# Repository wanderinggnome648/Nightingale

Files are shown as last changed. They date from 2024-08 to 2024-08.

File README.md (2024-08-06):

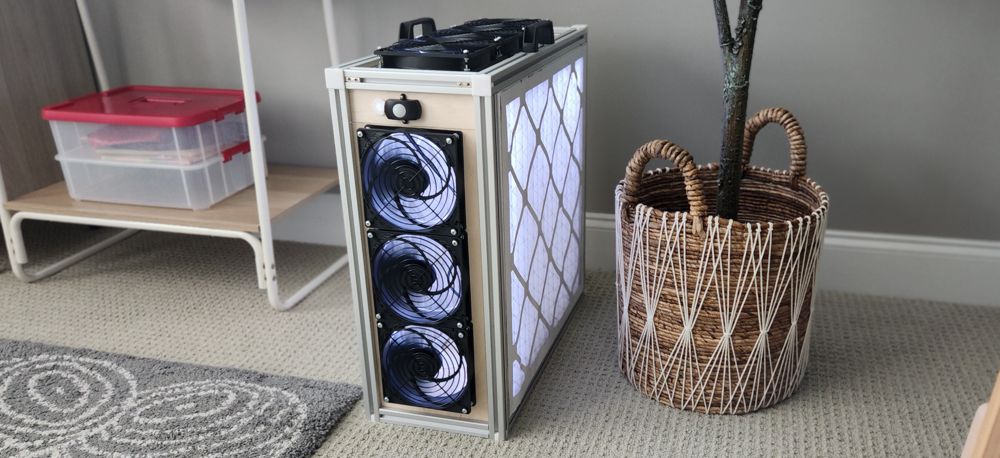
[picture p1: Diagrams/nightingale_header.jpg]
Product image


# The Nightingale: An Open-Source, Ultra-Quiet, Automatic, Permanent, Effective Air Purifier With Low Maintenance Costs

A PC-fan based air purifier design, the Nightingale's major features are:  
- **Effective**: Purifies air through two 20x20x2 MERV 13 air filters that are efficient at removing pollen, dust, and infectious aerosols, but have very high air flow.  
- **Ultra-Quiet**: No need to turn it down or off due to noise because you'll barely know it's running. Uses PC fans designed to push a high volume of air quietly. 
- **Permanent**: Uses a strong extruded aluminum frame that is a standard profile (1"x1") and easy to source from several manufacturers. 
- **Automatic**: Turns on when people are present and off when people leave. Always runs at max speed. Nothing to configure (or misconfigure). If it's plugged in, it's on. 
- **Visual Indicator**: Because the PC fans are so quiet, you might not even know it's on, so energy-efficient, interior lights indicate it is purifying. 
- **Easy Filter Change**: When you change the filters simply pop them off the side and replace. No disassembly required.
- **Cheap Maintenance**: No pricey filter replacement costs. Simply use standard MERV 13, 20x20x2 furnace filters commonly available in the US that cost around $10-$15 per filter (or less when purchased in bulk). Change yearly or after wildfire events. 
- **Standard Parts**: If you have a problem, you can fix it yourself. 
- **Open-Source**: No vendor lock-in. Build it. It's yours. 
- **Low Energy Consumption** Consumes only enough electricity for six PC fans and energy-efficient LED lighting. Turns off when the room is empty. 
- **Slim Design**: About the size of a desktop computer, it doesn't take up much space. 
- **Easy Wiring**: Uses standard connectors interior connectors (DC) that plug together. No soldering required.  

# Release Notes

## Version 1 - Baseline
Released on August 4, 2024. 

# Materials

You can likely do a better job sourcing materials in the quantity you need and obtaining a lower price. This is mostly just a list of all the items you would need to build a box and their approximate cost. 

## Aluminum Frame

Tnutz is a supplier of extruded aluminum. You can order specific lengths pre-cut. It takes about 5-8 days for processing. We use 1" x 1" T-slot frame, which is also known as 1010 T-slot frame. 

| Quantity | Type | Length | Fractional length | Total Length | Machining for one end | Machining for other end | Link  |
|---|---|---|---|---|---|---|---|
| 8 | 1"x1" | 20" | 0.500" |  20.5" | No machining | No machining | [LINK](https://www.tnutz.com/product/ex-1010/?attribute_pa_length-in=20&attribute_pa_fractional-length=0-500-1-2)
| 4 | 1"x1" | 7" | 0.063" (1/16) |  7.063" | No machining | No machining | [LINK](https://www.tnutz.com/product/ex-1010/?attribute_pa_length-in=7&attribute_pa_fractional-length=0-063-1-16)

## Panels 

We use 1/4" unfinished plywood for the panels because it's an inexpensive, durable material that is easy to find. You can source plywood in 4" x 8" sheets from any hardware store and then cut them down to manageable sheets using a table saw. Alternatively, MakerStock sources plywood in smaller sizes that is ideal for Glowforge laser cutting.  

| Quantity | Type | Thickness | Size | Cost/Piece | Link  |
| --- | ----- | ---- | ---- | -----  | -----  |
| 4 | Baltic Birch Plywood | 1/4" | 12x20 | $4.25/sheet |  [LINK](https://makerstock.com/products/baltic-birch-plywood?variant=32477598580833)  |

### Glowforge Laser Cutter
The Glowforge is a popular small laser cutter. The Glowforge size is slightly too small for the exact panel size that we need, so we break each panel into two parts -- the main part and a additional slat. 

See the LaserCut/SmallLaser folder for SVG files. Note that two of the panels are duplicates and so you need to cut them twice. 

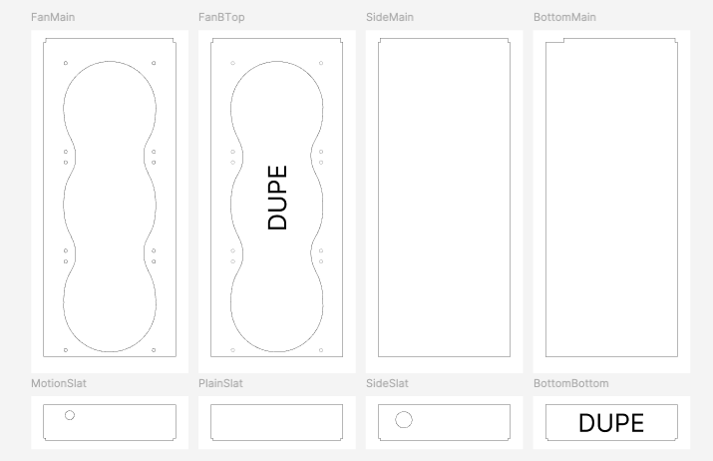
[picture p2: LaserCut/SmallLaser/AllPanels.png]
Diagram of all panels


To minimize burning of the material, we highly recommend covering the top face of the material with masking tape. Also, after cutting, we recommend sanding edges and inside the holes to eliminate the smoke smell. You don't want a purifier that smells like smoke!

Also, I'm not perfectly happy with the fit of the panels in the split design, and when I make my next few, I'll probably tweak the size a bit. It's tricky: Too big and you risk not fitting into the grooves. Too small, and it wobbles more than I'd like. Feel free to measure it yourself and iterate to get your perfect panel fit. If you find a better fit, let me know. 

### Large Laser Cutter
With a larger laser cutter, you can cut the entire panel in one piece. 
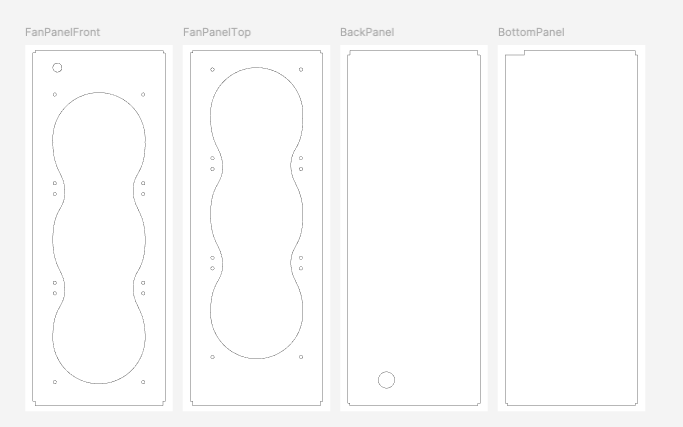
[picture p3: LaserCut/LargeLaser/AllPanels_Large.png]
Diagram of all panels


To minimize burning of the material, we highly recommend covering the material with masking tape. Also, after cutting, we recommend sanding edges and inside the holes to eliminate the smoke smell. You don't want a purifier that smells like smoke. 

### CNC
Instead of laser cutting, you can use a CNC to cut the panels. This is preferred to avoid having to sand off burnt material. Refer to the large laser cutter files for panel sizes or the primitives folder. 

*More instructions for CNC coming soon!*

## 3D Printed Components

Required
| Quantity | Item | Purpose | Filename | Image | 
| --- | ----- | -----| ----- | --- |
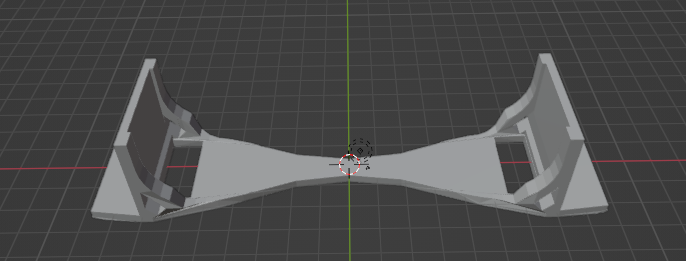
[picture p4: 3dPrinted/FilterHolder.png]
Filter holder
| 8 |  Filter Holder | Because the fans are mounted outside, the filter needs something to rest against | 3dPrinted\FilterHolder.stl | 

Optional
| Quantity | Item | Purpose | Filename | Image | 
| --- | ----- | -----| ----- | ---|
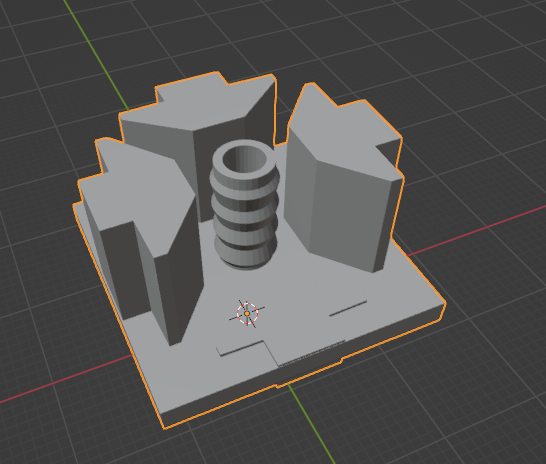
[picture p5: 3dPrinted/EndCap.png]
End Cap
| 8 |  End Cap | Cover sharp edges / protect scratches | 3dPrinted\EndCap.stl | 
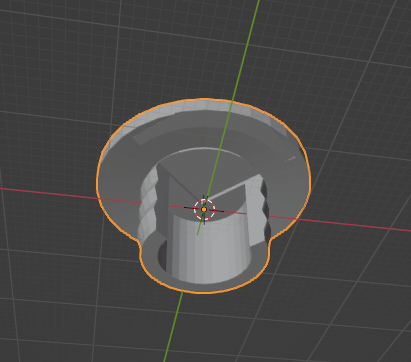
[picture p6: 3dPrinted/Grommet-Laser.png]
Grommet
| 1 | Grommet | Cover the hole where the motion sensor runs| 3dPrinter\Grommet-Laser.stl | 

NOTE: The end cap is a standard part and can be obtained elsewhere from TNutz, 80/20, and Amazon. Ensure the cap is 1"x1" (10 series, aka 1010). Also, you can get a rubber grommet from a hardware store.

## Interior Components 
| Quantity | Item | Description | Cost | Link  |
| --- | -----| --- | ---- | ----- |
| 1 | 5-Pack of Artic P14 PC Fans | Discounted pack of 5 fans | $35 | [LINK](https://www.amazon.com/dp/B07HC9ZWDN?psc=1&ref=ppx_yo2ov_dt_b_product_details) |
| 1 | Artic P14 PC Fans | Single P14 PC Fan (to make 6 total) | $16 | [LINK](https://www.amazon.com/dp/B07GZJY4TM?psc=1&ref=ppx_yo2ov_dt_b_product_details) |
| 2 | 3-pack of 140 mm fan grills | Covers the fan for safety | $9 | [LINK](https://www.amazon.com/dp/B01BW21DXC?psc=1&ref=ppx_yo2ov_dt_b_product_details)
| 1 | Adafruit DC Barrel Adapter | Using a 1" hole, this screws on the panel and provides a nice way to plug in the outside AC/DC power adapter | $3 plus shipping | [LINK](https://www.adafruit.com/product/610)
| 1 | AC/DC Adapter | Needs to be compatible with power where you are plugging it in (normally 110 volts in the US) and change to 12 volt, ~2 amp DC power | $5/each | [LINK](https://www.amazon.com/dp/B077PW5JC3?ref=ppx_yo2ov_dt_b_product_details&th=1)
| 1 | PWM Fan Hub | Connects all the fans to single power cable | $6 | [LINK](https://www.amazon.com/dp/B08C79CQH5?psc=1&ref=ppx_yo2ov_dt_b_product_details)
| 1 | DC Power 1 Female to 2 Male Y-Splitter | Splits DC power into two for lights and fan hub | $2 | [LINK](https://www.amazon.com/Splitter-Adapter-Y-Cable-Security-Parking/dp/B07J28SX6Y?th=1)
| 1 | PIR Motion Sensor | Activates the circuit when motion is detected | $6/each | [LINK](https://www.amazon.com/dp/B09PHHZMQN?psc=1&ref=ppx_yo2ov_dt_b_product_details)
| 1 | DC Extension Cable | Runs from the back of the unit to the front, where the motion sensor sits | $6 | [LINK](https://www.amazon.com/Power-Extension-Cable-5-5mm-Female/dp/B08176VFJ5?th=1) 
| 1 | DC to 4 Pin Fan Power | Converts DC power to 4 pin for the fans | $7 | [LINK](https://www.amazon.com/dp/B085S3Q7VH?psc=1&ref=ppx_yo2ov_dt_b_product_details)
| 1 | DC to LED light connector | Connects DC power to 2 pin LED lights that are 8 mm wide | $1/each | [LINK](https://www.amazon.com/dp/B01DM7F8O0?psc=1&ref=ppx_yo2ov_dt_b_product_details)
| 1 | String of 8mm LED lights | Any solid color, can be cut at specific intervals | $12 | [LINK](https://www.amazon.com/gp/product/B075LB9HK2/ref=ppx_yo_dt_b_search_asin_title?ie=UTF8&th=1)
| 1 | 20-pack of 1010 L-Shape Corner Connectors | Used to connect the aluminum pieces into a box | $28 | [LINK](https://www.amazon.com/dp/B09F67JQR1)
| 1 | 30-count M4 x 40-mm machine screws | To attach the grill to the fans and the fans to the panel, you need some relatively long machine screws. I think this is the right length to go the entire length of the fan. However, I did it the harder way with 2 screws and bolts per hole. If you find out 40mm is wrong (or you find the right imperial version, let me know) | $6 | [LINK](https://www.lowes.com/pd/Hillman-4mm-0-7-x-40mm-Phillips-Slotted-Combination-Drive-Machine-Screws-30-Count/999994818)
| 2 | 16-count M4 nuts | To attach the grill to the fans and the fans to the panel, you need some relatively long machine screws | $3/each | [LINK](https://www.lowes.com/pd/Hillman-4mm-x-0-7-Zinc-Plated-Steel-Hex-Nut-16-Count/999995424)
| 2 | Plastic Handle | Screws into the wood slot and makes carrying the unit easier. | $5/each | [LINK](https://www.tnutz.com/product/han-015/)
| 2 | Tiny wood screws | To mount the motion sensor into the wood panel, you need some very small screws. Recommended size is about <.5" in length. You likely have something already that would work.

## Filter
| Quantity | Item | Description | Cost | Link  |
| --- | -----| --- | ---- | ----- |
| 2 | MERV 13 20x20x2 Furnace Filter | Filter medium | $10/each | [LINK](https://www.amazon.com/gp/product/B0BL4XBTLN?th=1) |

Note: 20x20 furnace filters are NOT 20" long. They are always a little smaller. I designed this purifier to fit a filter with an actual filter size of 19 1/2" x 19 1/2". I do not know how much the furnace filter size varies by manufacturers other than the one above, but I do know most of them are smaller than 20". If your filter is bigger than 19 1/2" it likely won't fit this case. You can make the case a little larger while connecting with the l-connectors to accommodate, but at a certain size the panels won't fit. If the furnace filter is smaller than 19 1/2", probably not a big deal as you can always add foam tape to the outside to get a more snug fit. 

## Other Parts and Tools
- Screwdriver - Connecting the fans to the panels
- Rubber mallet - Helps get stuff to fit snugly w/o damaging it
- Wood Glue - For affixing the filter holders
- Utility knife - Cutting zip ties, opening packages
- Sandpaper - Removing lasercut edges
- Cable ties - Organizing the wiring

# Assembly
1. Take four of the 20.5 aluminum pieces and assemble into a square using the L-shape connectors on the side corner (see diagram). Do the same for the other four 20.5 aluminum pieces. Tighten the screws, but not too tight, because you'll loosen them later. 

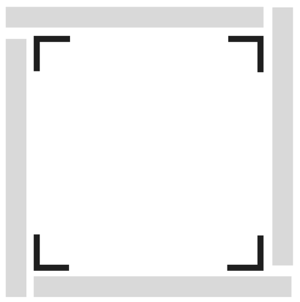
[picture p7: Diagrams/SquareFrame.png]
SquareAssembly


2. Connect the four 7.063" cross beams to form a cube. You use the same L-shape connector as you did earlier, however, you need to configure it in a slightly different way, which puts most of the L-shape connector on the outside of the cross beam. This orientation leaves more space inside the grooves for panels. Tighten all these l-connector screws. No need to overtighten them. (NOTE: We'll untighten one of the l-connectors at the end for the final panel). 

Also, make sure the two squares you made in Step 1 are oriented in the same way with respect to each other (see panel order diagram below)

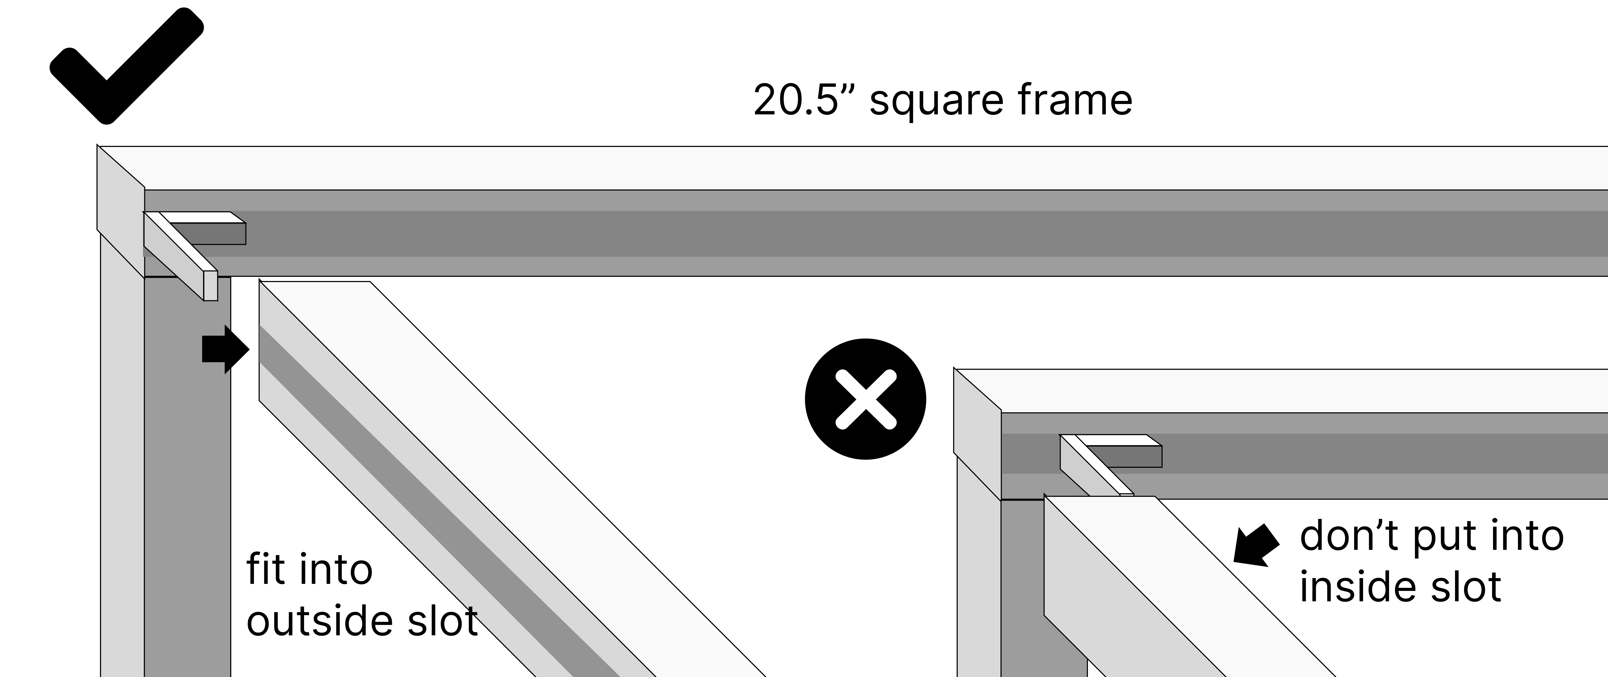
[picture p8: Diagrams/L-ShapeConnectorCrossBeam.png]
LConnectorCrossBeams


3. Add the panels in the sequence shown from 1 to 4. Arrows indicate distinguishing parts of the panels. 

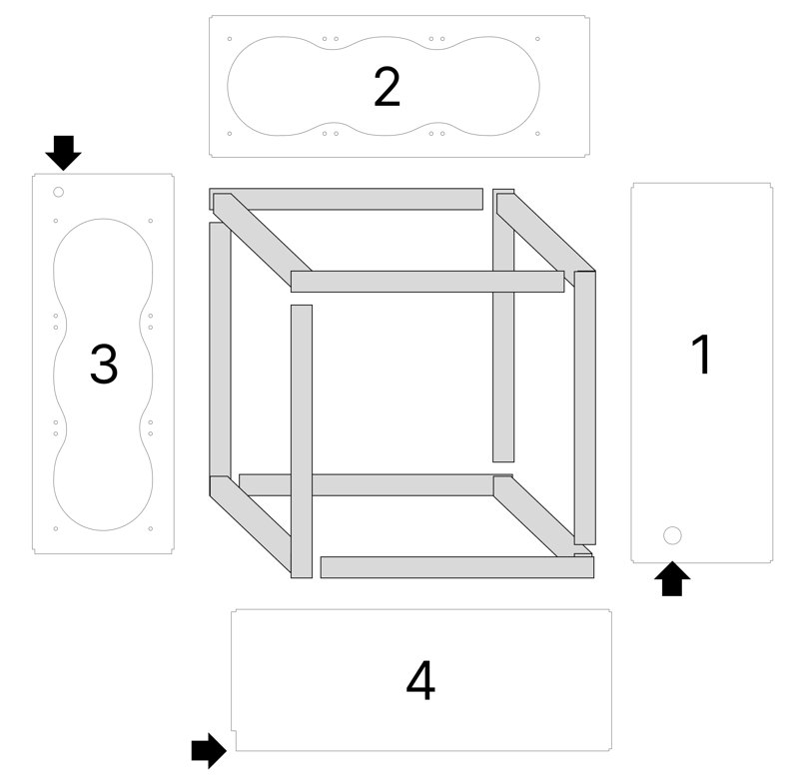
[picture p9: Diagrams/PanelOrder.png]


For panels 1-3, you will loosen the specified screws underneath where the panel will go (note: the panel is already inserted in the image). 

Where to loosen screws

When you loosen these particular screws, a U-shaped portion of the frame will slide out, allowing you to fit the panel inside the grooves and slide back into place.

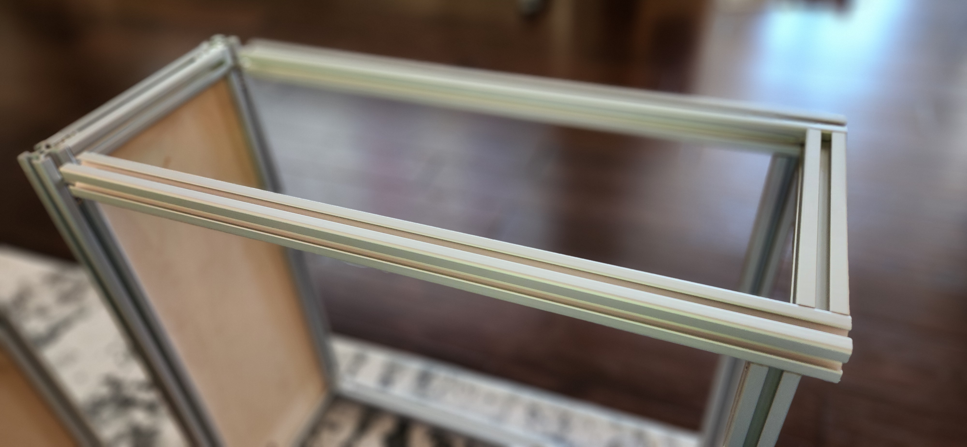
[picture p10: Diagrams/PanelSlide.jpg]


Also note that the corner spaces inside the grooves are different on each side. On one side, the corner is free of any L-shape bracket and has more space (see below). 

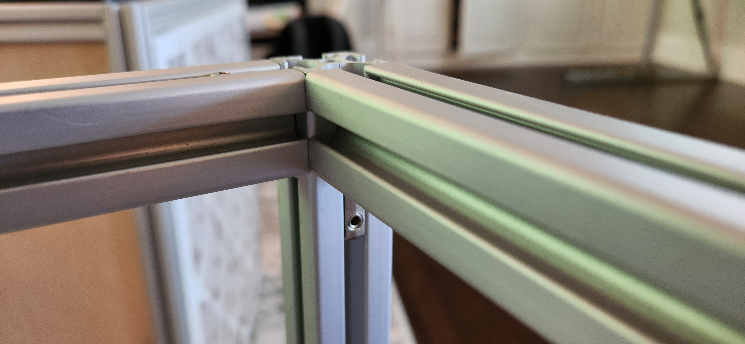
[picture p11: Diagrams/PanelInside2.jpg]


On the other side, there is a small part of L-shape bracket visible (see below). 

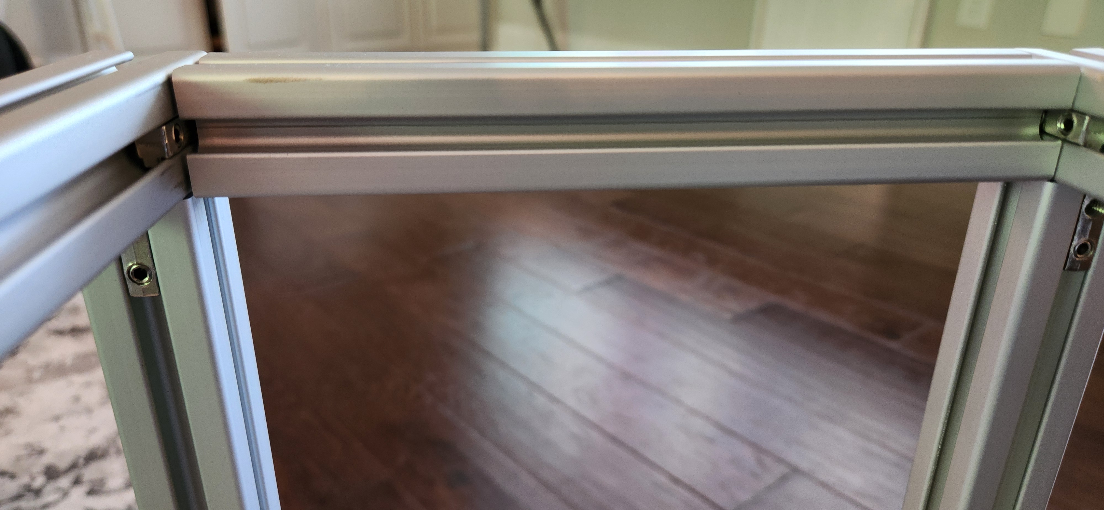
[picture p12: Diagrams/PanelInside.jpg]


Be sure you have the panel corners matching to the right interior corners for it to fit properly. Once you have the orientation correct, you can slide the U-shape frame back into place and re-tighten the screws you loosened. You can then move to the next panel section. It's a bit like a puzzle. You can add panels only in one direction, but not the other because the panel will keep the frame from sliding out if you go the wrong way.

4. On the final panel, you have to only loosen the screws on one side beam as shown. This allows one beam to slide out and you can add the final panel and tighten. Note that this panel is specifically cut to allow you to tighten the right screw after the panel and beam has slid back into place. 

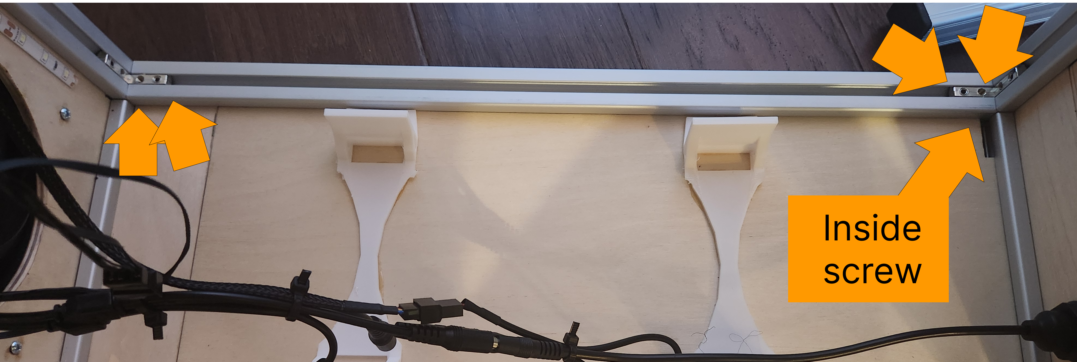
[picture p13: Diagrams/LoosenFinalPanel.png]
Last panel


5. Add the PC fans to PC fan panels using machine screws and bolts. For each fan, it should sit outside the frame, with the logo pointing inside (NOTE: This is counter-intuitive. The PRETTY side, i.e., the side with the nice company logo, points INSIDE), and a grill covering the outside. Ensure the connecting wires are inside the box. Try to arrange the fans so the fan wires are mostly together, which will make it easier to wire later. The machine screw should have the head outside on the grill, go through the grill hole, the fan, and the panel. Put the nut inside to hold it together. Add a washer if you like to protect the wood. (Note: In the diagram, I'm using 2 shorter screws + nuts, so just ignore that. I think 1 longer screw + 1 nut is better as it's fewer screws and easier to assemble.)

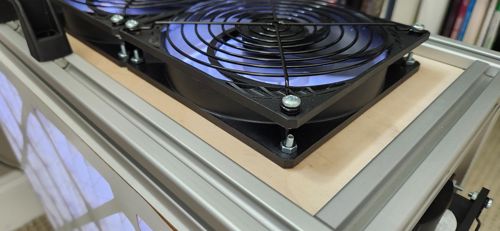
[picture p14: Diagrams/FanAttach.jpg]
Attaching the fan


6. Now take the 3D-printed filter holders and glue them with wood glue inside the box. The filter holders give the filters something to push against and also give you a place to use a zip tie to organize the wiring. Each panel should have two filter holders. Glue two at a time and cover with a heavy book until the glue dries. Then rotate the box 90 degrees and glue two more. (Images shown with wiring, which you haven't done yet).

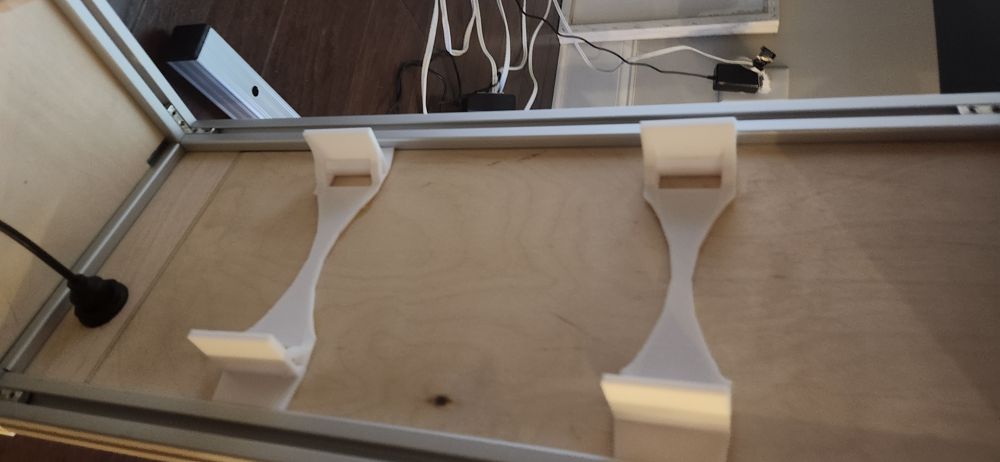
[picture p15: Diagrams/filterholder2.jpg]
Filter holder over plain panel


The filter holders also fit as shown over the fans, the gap in the filter holder is where the connection screws go. For the panels with fans, only apply glue to the *ends* of the filter holder, not the middle (so you don't add glue to the fan, if you need to replace it later).

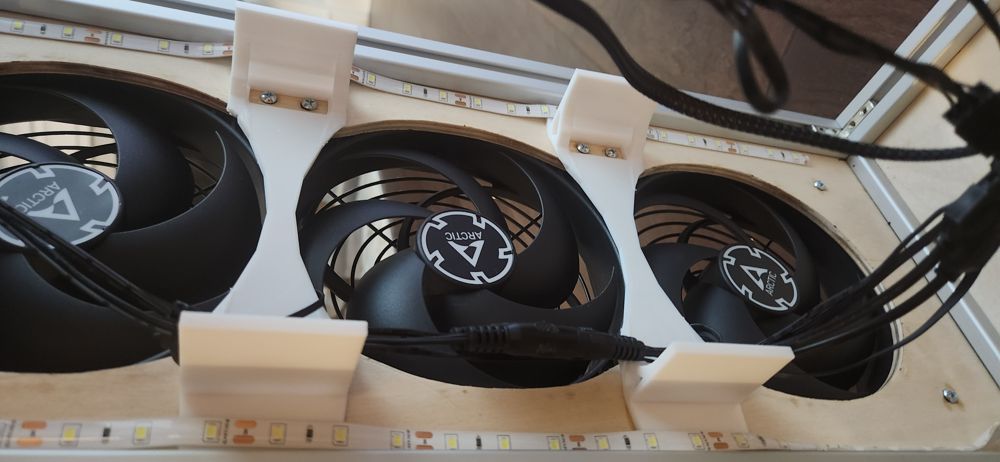
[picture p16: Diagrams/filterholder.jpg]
Filter holder over fans


7. Now we can start to add the wiring. You'll screw the DC Barrel into the panel where there is the larger 1" hole on an otherwise bare panel (the first panel you added). 

A high-level schematic of the wiring is here: 

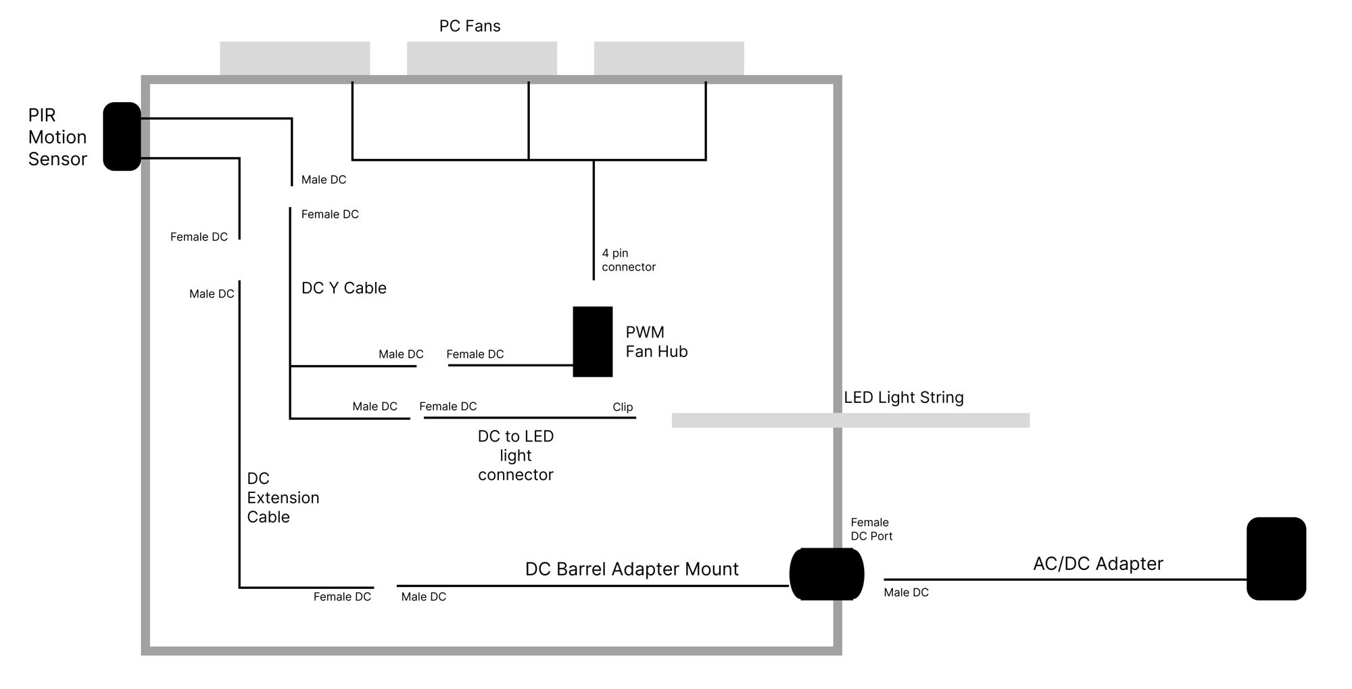
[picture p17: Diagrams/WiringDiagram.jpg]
Wiring diagram


8. Daisy-chain the fans together as much as you can. The five-pack of Artic fans should have extra ports to connect one fan to another. Daisy-chaining them saves you ports on the PWM Fan Hub and makes organizing wires easier, but you can always run the fan directly to the PWM Fan Hub. 

9. Connect the DC extension cable to the DC Barrel Adapter Mount inside. The PIR Motion Sensor should be on the outside with cables running inside through the small hole. One cable will connect to the DC extension cable and the other will connect to the DC Y Cable. From the Y Cable, you'll split into LED lighting and the PWM Fan Hub. All the fans will connect to each other and the hub.

10. For the LED lighting, I like to run it on the panels with fans in a figure 8 pattern around both panels, sticking to the 1/2" gap between the panel and the filters, where it won't get in the way of the filters when inserted(see below). This provides indirect lighting when activated, giving the unit a glow. 

Filter holder over fans

11. Ensure all the wiring is connected and nothing is near the fans. Plug in the AC/DC adapter in to test the wiring. Check for the following
- The unit should come on when the PIR sensor detects motion. 
- The PC fans should all blow air outside, not inside.  
- All the fans are spinning when motion is detected.
- Adjust the PIR motion sensor on the back of the unit with a screwdriver to maximum sensitivity/duration. This ensures it will come on quickly and stay on for a few minutes.  

12. If you're confident the wiring is correct, you can zip tie everything down to the holes on the filter adapter. Make sure that you've tied it down so that the DC connections won't easily come loose and that the wires won't move and get into the fan blades as the unit is being moved around. 

13. Tighten all interior L-shape connectors sufficiently (no need to over tighten it).

14. Press the 20x20x2 furnace filters into the square side. The airflow is from outside to inside through the filter. The metal supports on the filter should be inside. 

15. Add the 3D printed grommet (or one from a hardware store) to the PIR sensor hole. If you want, you can cover the small hole in the bottom panel with a piece of tape. 

16. Add the handles to the T-slot on the top of the unit as shown in the first picture.

17. Also, you can add the end caps to the aluminum ends so that you don't scratch flooring or people. Once you add the end covers, you can't add anything else to the T-slot, so this is really the last step everything has gone well so far. 

18. Plug the unit in and ensure the PIR sensor is pointed at where there is most likely to be people, so it can come on when people are present. 

## FAQs

### Q: Why buy this instead of HEPA? 

- A: A HEPA filter is originally based on [World War II gas masks](https://en.wikipedia.org/wiki/HEPA), which explains the high efficiency. However, the high efficiency/low airflow is a disadvantage when purifying a room. HEPA purifiers tend to be big, loud, and have costly filter replacements. Furnace filter-based designs that use PC fans are an amazing combination of quiet and highly effective. 

### Q: What's the ideal environment for this design?

- A: I designed this as the purifier I would want in my kid's classroom. In particular, I want to be able to tell my kid to make sure the purifier is running, which is obvious from the LED lighting. Also, I don't want teachers to worry about turning it off/on or changing the speed settings. Finally, I wanted it to be durable, easy to fix if a component breaks, and easy to replace the filters. 

- In cases where classroom space is limited, we're exploring whether we can mount this unit to a wall with aluminum stand-offs. A wall-mount option could save space and keep people from accidentally turning it off. 

### Q: Why is it named 'The Nightingale'? 

- A: [Florence Nightingale](https://en.wikipedia.org/wiki/Florence_Nightingale) (1820-1910) was an activist, statistician, and the founder of modern Nursing. In her book, [*Notes on Nursing: What It Is, and What It Is Not*](https://archive.org/details/notesnursingwhat00nigh/page/6/mode/2up), she writes: 

> The very first canon of nursing, the first and the last thing upon which a nurse's attention must be fixed, the first essential to the patient, without which all the rest you can do for him is as nothing, with which I had almost said you may leave all the rest alone, is this: **TO KEEP THE AIR HE BREATHES AS PURE AS THE EXTERNAL AIR, WITHOUT CHILLING HIM.** 

### Q: What is the clean air delivery rate (CADR) of this unit? 

- A: I haven't tested it yet myself or had it tested by a reputable third party. Having similar dimensions and PC fan design (six P14 Artic PC fans) as the Nukit Tempest, it should have a similar CADR. 

## Future Directions

Some changes I'd like to make in the future ... 

- Tweak the panel size to better fit in the grooves w/ no slack. 
- Use a CNC instead of laser cutter to make full-size panels w/ no sanding. 
- Iterate on the design based on feedback. 

## Acknowledgements

- [Corsi-Rosenthal Box](https://en.wikipedia.org/wiki/Corsi%E2%80%93Rosenthal_Box): In 2020, Corsi and Rosenthal popularized a simple DIY air purifier for removing airborne infectious disease using a box fan, furnace filters, and duct tape. At the time, the idea that a MERV 13 furnace filter, which has only [85% efficiency with tiny particles](https://www.ncbi.nlm.nih.gov/pmc/articles/PMC7127325/) could be better than HEPA filtration which has 99.99% efficiency seemed controversial. However, the key insight was that MERV 13 furnace filters had much better airflow than HEPA filters, which meant the total amount of clean air was much more. Disadvantages of the CR Box was only that it takes up space, the box fan can be louder than ideal for a classroom, and it's a temporary solution made with duct tape and is not extremely sturdy. [The Corsi-Rosenthal Foundation](https://corsirosenthalfoundation.org/) is a non-profit dedicated to promoting clean air and provides support to related charitable projects. 

- [Nukit Tempest](https://cybernightmarket.com/products/the-nukit-tempest-air-purifier-kit): An innovative and durable DIY air purifier design, the Tempest is made of metal and highly resembles a PC case. It's sleek and black, the six P14 fans are mounted inside, and it also takes 20x20x2 furnace filters. Overall, a near perfect design. Its only weaknesses are that you need to slightly disassemble the unit to replace the air filters, and you may not be able to tell that it's plugged in and running (because it's so quiet). Estimates are around 260-280 CFM. [A highly-recommended design](https://housefresh.com/nukit-tempest-review/) for situations where you want durable, simple, and ultra-quiet air cleaning. 

- [AirFanta Pro](https://www.amazon.com/AirFanta-based-Rosenthal-Purifier-3813ft2/dp/B0CJTYWQBT): Amazingly powerful and compact design using custom filters and PC fans, the 3Pro gets 430 CFM at full speed. It has a configurable adapter, which means if you don't mind the noise, you can crank it to max. However, if you want to limit the noise, you can lower the power. Importantly, this purifier is extremely portable -- you can pack it up inside a suitcase and take it with you. It's an absolute steal at $150, especially considering the amazing cleaning power. I own several of these and enthusiastically recommend them to others. In particular, in schools where noise might not be as much of an issue (e.g., cafeteria, common areas), I think this is likely the best bang-for-the-buck. In classrooms, you can also purchase two of them and turn them to half speed.

- [CleanAirKits](https://www.cleanairkits.com/): The original DIY purifier kit builders, they offer many kit models with a lot of cleaning power using ultra-quiet PC fans. They've researched a ton of different PC fans and identified the good ones. I own several Tower of Power models and have recommended them often to friends. In fact, a luggable protects my dad when he's in the office meeting people. 

- My friend Tony, who recommended I check out aluminum frames for air purifiers and provided feedback.

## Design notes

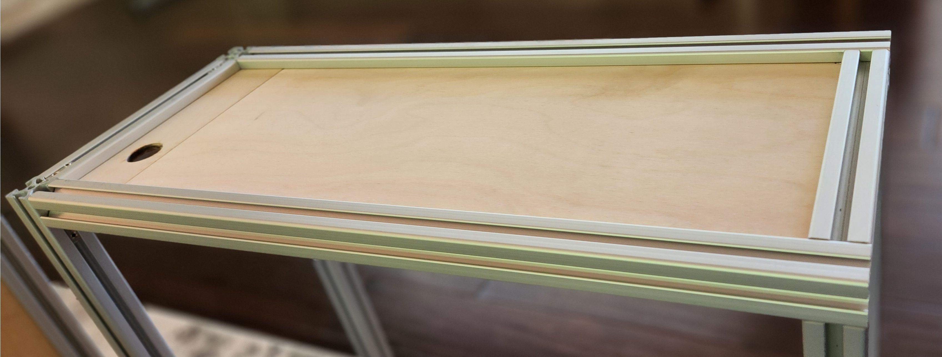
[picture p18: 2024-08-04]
Diagrams/PanelClosed.jpg

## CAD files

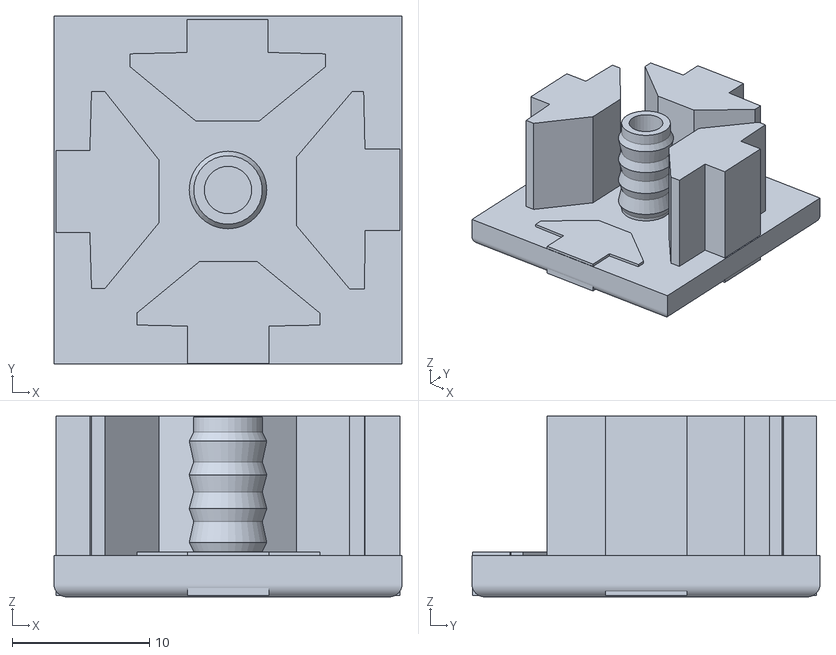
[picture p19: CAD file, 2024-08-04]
3dPrinted/EndCap.stl
25.4 x 25.4 x 13.2

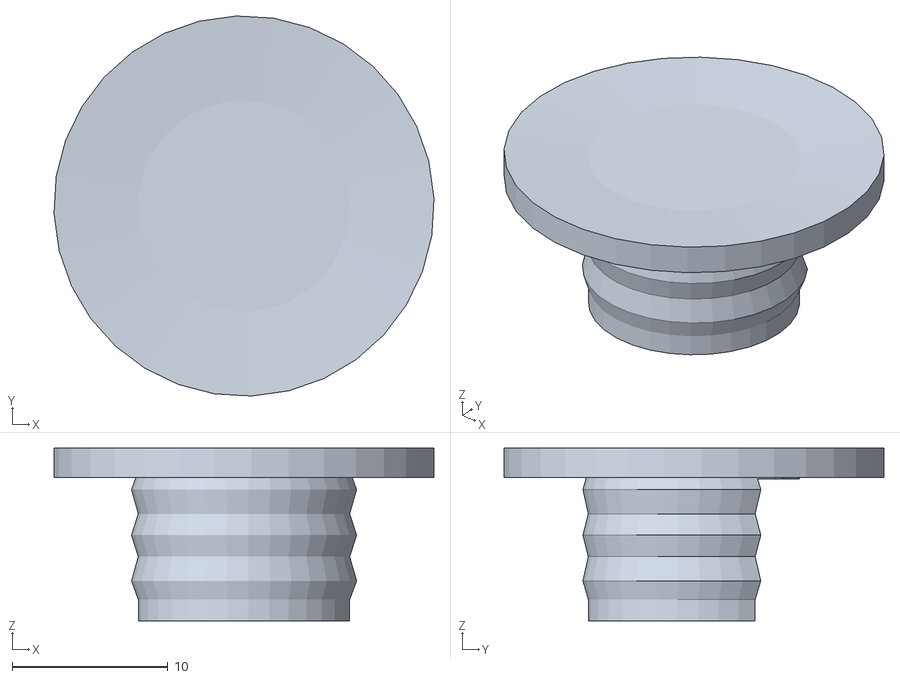
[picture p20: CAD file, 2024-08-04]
3dPrinted/Grommet-Laser.stl
24.4 x 24.4 x 11.1

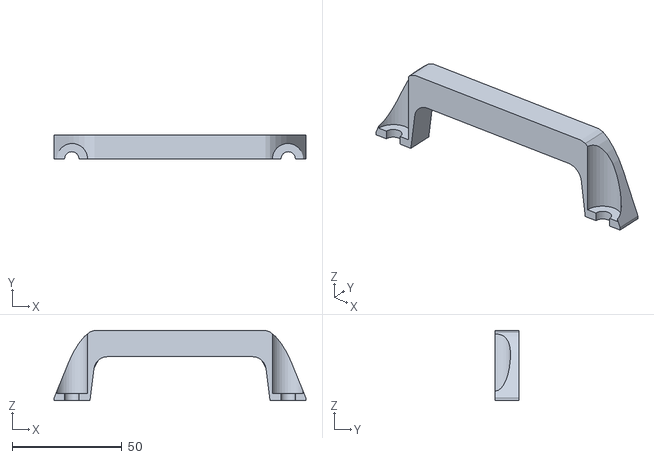
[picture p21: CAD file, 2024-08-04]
3dPrinted/HandleHalf2.stl
115.0 x 10.8 x 32.0

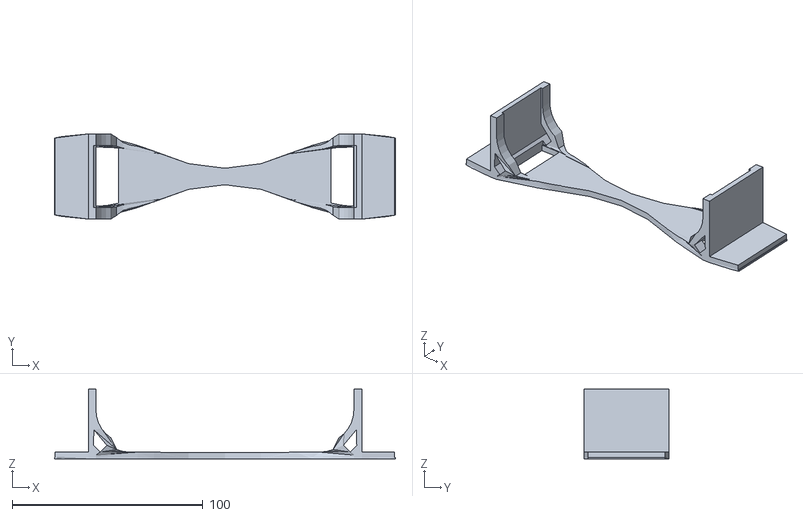
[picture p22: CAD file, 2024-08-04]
3dPrinted/FilterHolder.stl
178.7 x 44.7 x 36.5

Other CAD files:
3dPrinted/HandleHalf.stl

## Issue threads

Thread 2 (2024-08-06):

Feedback

raccettura, 2024-08-06:
This looks pretty good.

Wasn't sure the best way to provide some feedback, so figured I'd just open an issue...  I've been looking into building something similar but perhaps 8 fans and using an esp32 running @esphome to make the fan speed something that could be controlled and monitored via @homeassistant.  A few thoughts popped up aside from sizing:

1. Why not move the fans inside the case and put the fan guards on the exterior?  That would certainly improve the "curb appeal" of the device.
2. Why not add some weather seals around the air filter for sure, possibly also the fans?  That would ensure more airflow is going through the filter rather than around it and should improve effectiveness.

wanderinggnome648, 2024-08-06:
Cool. No worries, I'm actually still learning these interfaces, too. Few thoughts.
1. My early designs put the fan inside, where it's also convenient for the fan to rest against. I changed it after some early designs that seemed like they should have been good weren't that good using the salt crystal particle counting method (shoot pure salt water in the air with a nebulizer and then track with a particle counter how quickly your purifier removes it in a confined space like a bathroom. I am not a fluid dynamics expert, but after many iterations and comparing against other purifier designs, I learned that the interior size needed to be minimized. Also, I learned that I couldn't just deck out the box with fans, but in certain positions (e.g., across from each other), they interfered. I also found a few papers and tweets on similar topics. On the fan placement inside vs. outside, I guessed that outside might be superior based on the Air Fanta 3Pro's design. My suspicion is that pulling the air out is better than pushing it out, but I haven't confirmed this in a head-to-head test. But that's why I decided to default to outside and use the 3d printed holder on the interior. To be clear, it's a guess.
2. Again, earlier in my tests I did a lot of sealing with tape and foam when I believed that was a problem. Turned out, it was my designs that were bad and the sealing didn't matter. At the moment, I don't think I'm losing a ton of air through the small gaps. However, when I do my close-to-final test, I'll probably try that, too, to see if it makes a difference. Other makers in this space seem to have the same belief -- as long as the design is decent, the small gaps don't seem to matter.

On the monitoring/speed control, I love programmable microcontrollers and I debated on whether or not something like that was useful. For my specific use case of something for classrooms, I've avoided adding anything extra due to cost. What I may consider down the road is LoRaWan for monitoring. My rationale is that for schools, I want to know that it's being used, but I can't trust (or expect) the school to give my purifier wifi access. So, instead, I can just broadcast the stats via LoRaWan and have a nearby parent save and relay the data. So, my only thoughts for microcontrollers are just thinking through your use case and whether you might want to scale it up and just make sure it makes sense.

On the multiple fans, my advice is to mock up different designs with cardboard, fans, filters, and duct tape. And do quick tests with salt particles to see how well it works. It was humbling for me to see good design ideas I had didn't work well in practice. The Corsi box design (and AirFanta 3Pro) works well (to my current understanding) because it's a box with a lot of filter area, somewhat minimized interior space, and all the fans on one side pulling in the same direction. The Tempest 6 fan design (3 fans at right angles) seems to work well because it's a good amount of filter area, minimized interior space, and 6 fans pulling in non-competing directions.

Hope that helps and good luck with your builds.

raccettura, 2024-08-06:
Thanks for the info.

Researching I've also seen cleanairkits's "luggable" designs which are pretty similar but 120mm internally mounted fans.  That's a bit cleaner of a design, but looks somewhat flimsy, I like the frame you're using, and definitely would want to go that route. My current thinking is to combine the two approaches with internally mounted fans. Their CADR seems pretty impressive based on the data in their [faq](https://www.cleanairkits.com/pages/frequently-asked-questions) leading me to believe it should work if the design is snug enough.

wanderinggnome648, 2024-08-06:
Yes, the sturdiness of the frame is a downside. I have 2 towers of power and my dad has a luggable. If nothing else, a sturdier frame is a huge win. Big thing for me was thinking long-term about airborne infectious disease, rather than short-term, and a durable frame is a big part of that.

It should definitely work, whether mounted inside or outside. It's probably worth a least a blog post or academic paper doing a head-to-head comparison. I will say that the Air Fanta 3Pro guy is an expert in water dynamics (@engineerwrong is his handle), and applied his knowledge to air. The AirFanta 3Pro has some weird and surprising magic that makes it have such a high CFM. I don't fully understand how much is attributable to the filters, the higher RPM/static pressure fans, the interior space, all fans on the same side, or interior vs. exterior mounting. But he's racked up the best CFM/$, so he's one to learn from. I wanted to hit 300-400 CFM on a single unit, but I couldn't pull it off without making it more boxy.

wanderinggnome648, 2024-08-06:
Also, when comparing the advertised results, keep in mind that all manufacturers report numbers which can vary. The best way I iterated was the same room, same setup, and just trying a lot of different designs quickly. It didn't matter whether my calculation for CADR was accurate, because I was just looking for relative comparisons. I'll likely send my box to the HouseFresh guy to put in his room for quick sanity check before I get too far down the road. It costs $$$ for the 3rd party test, but before I do that, I want to have high confidence I've optimized it well before doing so.

raccettura, 2024-08-06:
Apparently part of that magic is the custom filters, higher pleat count = more surface area = less static pressure required.  Plus some apparently pretty loud fans.

wanderinggnome648, 2024-08-06:
I haven't fully formed on opinion on making custom filters or not. They apparently aren't hard to have manufactured. But most vendors want to have custom filters and then mark them up a lot for on-going revenue. Schools end up tossing purifiers when the filter changes get expensive. So, I feel like for schools, the maintenance plan needs to be standardized/open.

raccettura, 2024-08-06:
I’m of the opinion proprietary things suck, especially when standards exist.

I’d rather go taller. There’s no rule an air purifier needs to be square, and space above is unused.

raccettura, 2024-08-06:
I was actually looking at 20x25, which seems pretty popular and 20x20 = 400 while 20x25 = 500.  That's a pretty substantial upgrade for slightly more height even with the same filter thickness.  Or 20x24x4.  The slightly taller height likely doesn't matter as you're not putting anything on top due to the fans being there.

That's a lot more surface area to pull air through which should improve efficiency.  Also more surface area that has to be saturated before filters need to be replaced, which in theory lowers cost, and still standard sizes you can find with a variety of vendors https://filti.com/product/7500-home-filter/ . So no proprietary bullshit.

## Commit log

2024-08-04 Adding baseline project
    [EndCap.stl, FilterHolder.stl, Grommet-Drill.stl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]
2024-08-05 Added note on machine screws
